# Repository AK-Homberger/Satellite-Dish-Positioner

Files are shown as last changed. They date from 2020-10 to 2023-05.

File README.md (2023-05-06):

# Satellite Dish Positioner

This is an automatical satellite dish positioner with an ESP8266 D1 Mini, a compass and an MPU. It controls the satellite dish direction with a Diseqc rotor (azimut) and a linear actuator (elevation). It uses an gyroscope device for elevation and a compass device for azimut control.

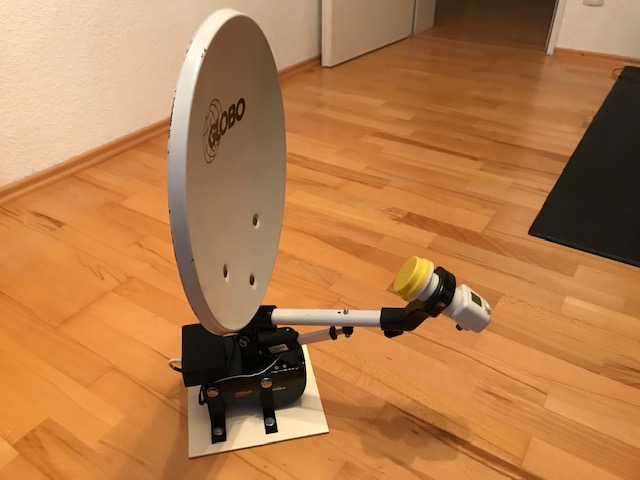
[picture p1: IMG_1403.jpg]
SatPositioner


The purpose of this device is to support me on the boat with the positioning of the satellite dish from the cabin. But it is also usable for campers and mobile homes.

## Hardware
The rotor is a standard Diseqc dish motor for less than 50 Euro. But for this project we use the motor upside down to move the dish in horizontal ballance. We have to remove the cranked dish connection tube from the motor. But keep the bolt and the nut. We need them to connect the upper and lower 3D-printed joint parts. 

The ESP8266 (in D1 Mini) controls the Diseqc motor with 22 kHz tone signals as defined in the [Diseqc specification](https://www.eutelsat.com/files/PDF/DiSEqC-documentation.zip) (see bus_spec.pdf, section 5 and also positioner_appli_notice.pdf). The ESP8266 generates the signal which has to be modulated on the coax signal line of the motor. I found the necessary circuit and signal generator code on GitHub:(https://github.com/acrerd/Arduino-Diseqc-solar-tracker). Many thanks for the helpful support. That saved me a lot of time. For simplification, I only used the right part of the [circuit](https://github.com/AK-Homberger/Satellite-Dish-Positioner/blob/main/diseqc-interface.pdf) starting with the 100 Ohm resistor. The risistor is directly connected to port D5 on the D1 Mini. This is sufficient to generate a signal that the Diseqc motor is recognising.

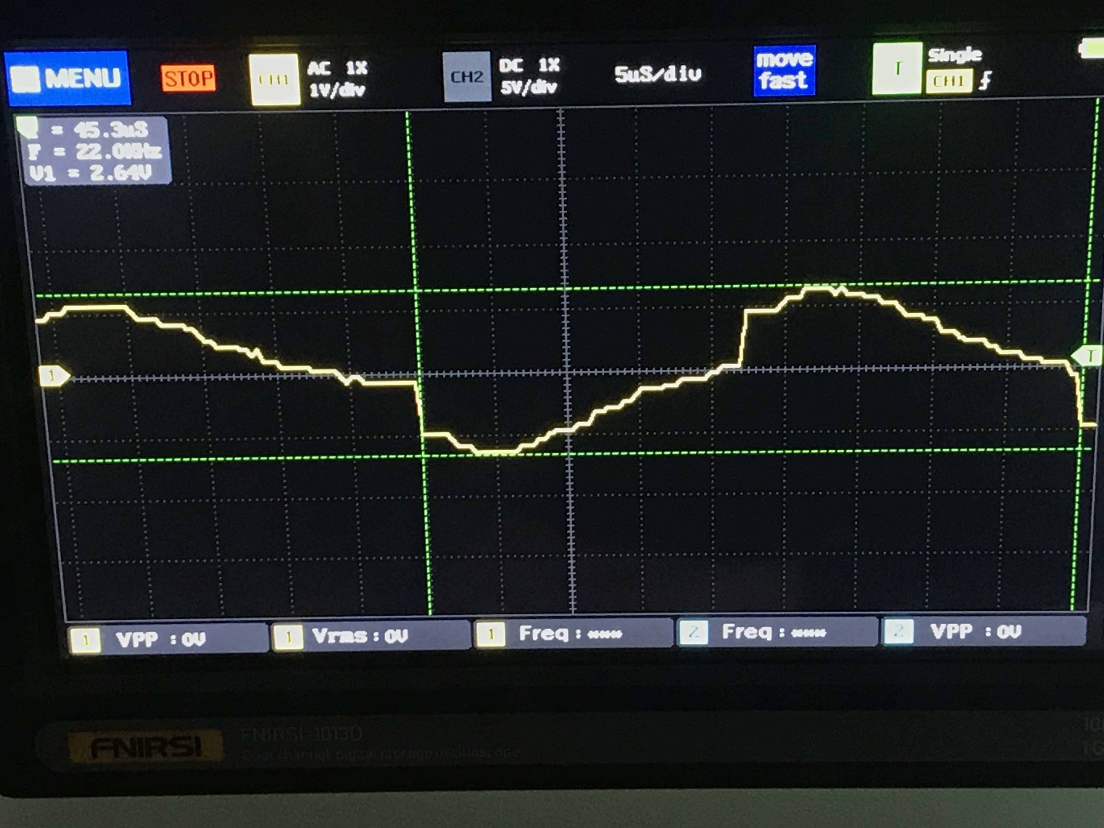
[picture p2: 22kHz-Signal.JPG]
22KhZ-Signal


The delay values in the Arduino code ( functions write0() and write1() ) had to be adjusted for the faster ESP8266. The delay with 21 microseconds works perfectly to generate a 22 kHz signal.

The motor gets the 12 Volt power via the coax connection. Be careful with the coax connector when the device is powerd. A shortcut between core and shield would instantly destroy the inductor coil (it can only handle about 300 mA).

The motor is able to move from -75 to +75 degrees with an accuracy of 1/16 degree. That is more than sufficient for positioning the azimut.
You just have to position the sat finder in a general south facing direction. Thats all.

The elevation is controlled with a standard small linear actuator which is available for less than 30 Euro. I use here an actuator with 50 mm length. But 25 mm should work also.

In addition to the 22 kHz logic, only four other items are required:

- Step-down-converter 12V to 5V: D24V10F5
- Compass: GY-271 from AzDelivery (install [QMC5883LCompass](https://github.com/mprograms/QMC5883LCompass) library in Arduino)
- 6 axis gyroscope: GY-521 from AzDelivery (install [TinyMPU6050](https://github.com/gabriel-milan/TinyMPU6050) library in Arduino):
- Motor driver:  Adafruit DRV8871 DC Motor Driver

**Be careful with the GY-271 from other sources. Some devices are using a HMC5883L compass instead of a QMC5883L. We need the QMC5883L for this project.**

The compass and the gyroscope are connected to the I2C bus of the D1 Mini (using D1=SCL and D2=SDA). The compass is inside the box on the pcb. The gyroscope is connected with a short 4-wire cable and placed on the back of the satellite dish.

The motor driver is using ports D0 and D6. The 22 kHz signal is generated on port D5.

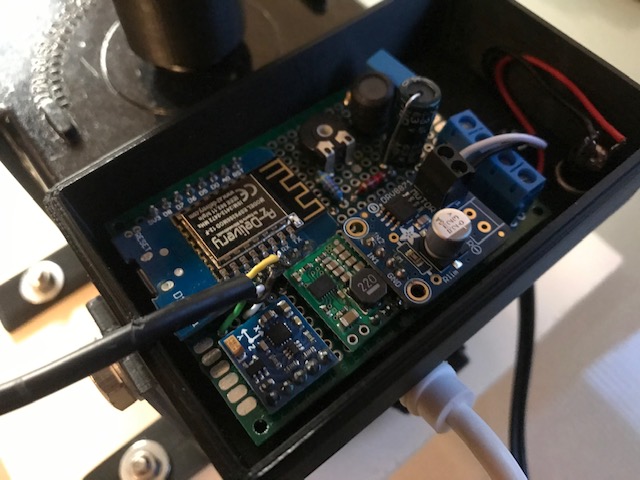
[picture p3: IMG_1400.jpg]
Circuit


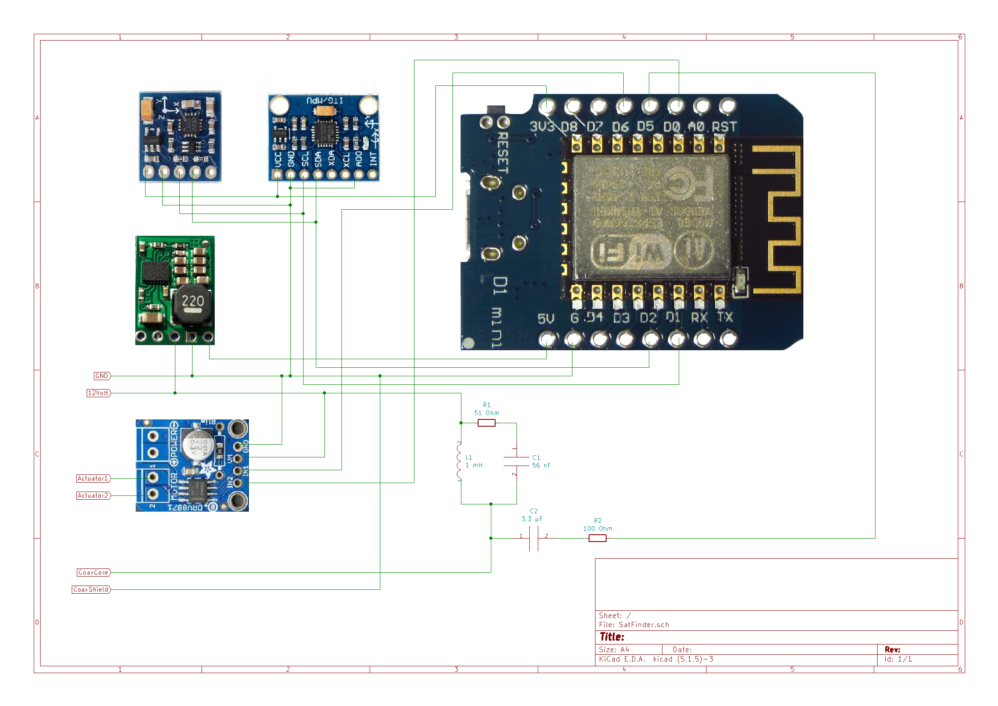
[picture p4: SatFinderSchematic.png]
Schematic


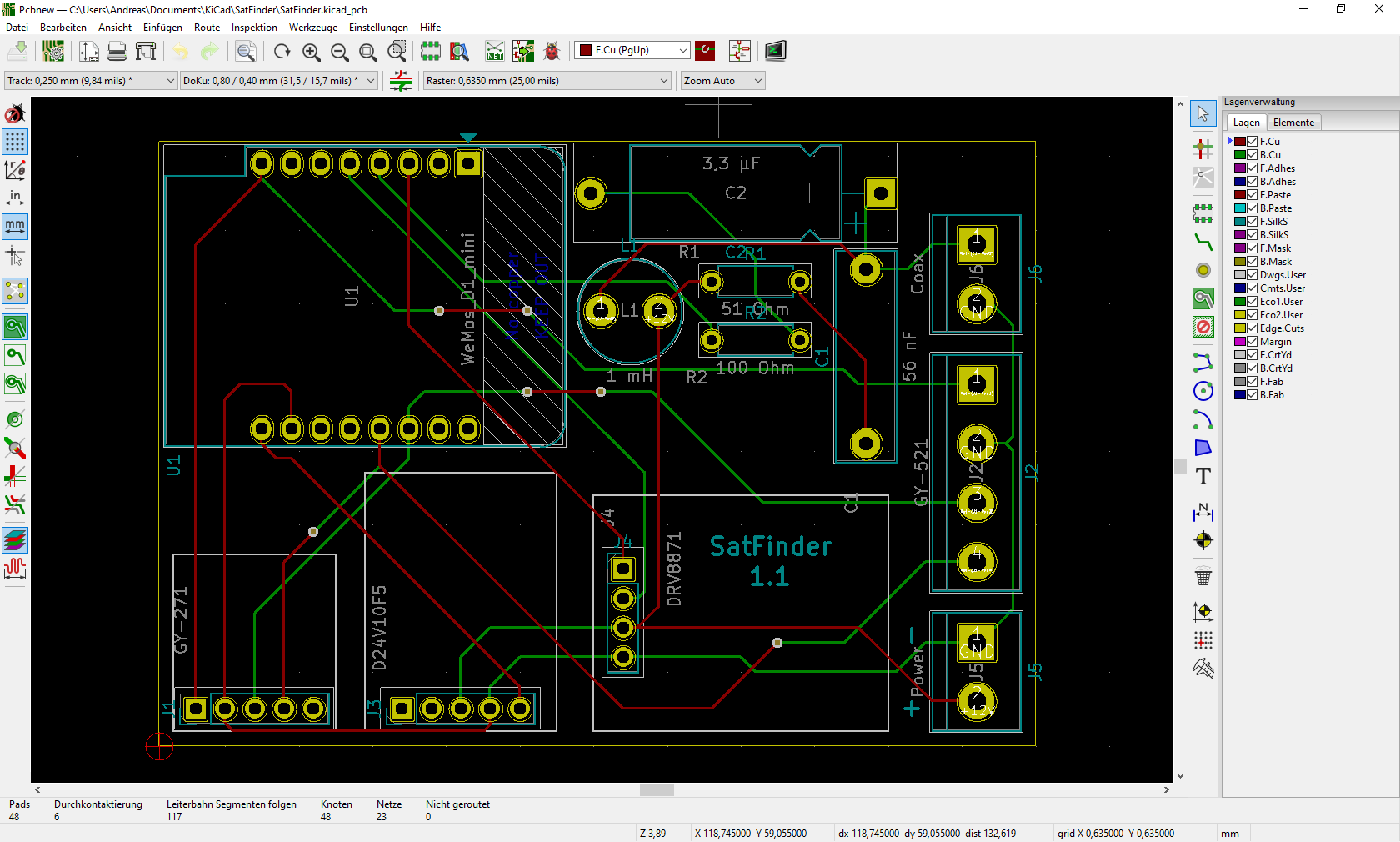
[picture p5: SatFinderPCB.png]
PCB


Schematics and PCB layout is in KiCAD folder.

## Software
The positioner is controlled with a web interface. The ssid and password for WLAN has to be set in the code.

The device is pre-configured for Astra 19.2 and my home location. Please change this for your location and satellite.
You can use one of the free calculators to get the angles for your location and desired setellite (e.g. https://www.satlex.us/en/azel_calc.html). Use "Azimut angle" and "Elevation angle". 

The true north azimut angle needs to be corrected (Az_Offset) to match the magnetic north of the compass (sailors should know how to calculate) and to correct a possible placing error on the pcb. 

The elevation angle must be corrected (El_Offset) with a dish specific value. For my dish this is -18 degrees between dish beam angle and angle of gyroscope mount. The offset has to be calculated only once and defined in the program.

```cpp
//Enter your SSID and PASSWORD
const char* ssid = "ssid";
const char* password = "passwod";

float Astra_Az = 164, Astra_El = 30.19, El_Offset=-18, Az_Offset=-10.0;   // Astra 19.2 position and dish specific offsets
```

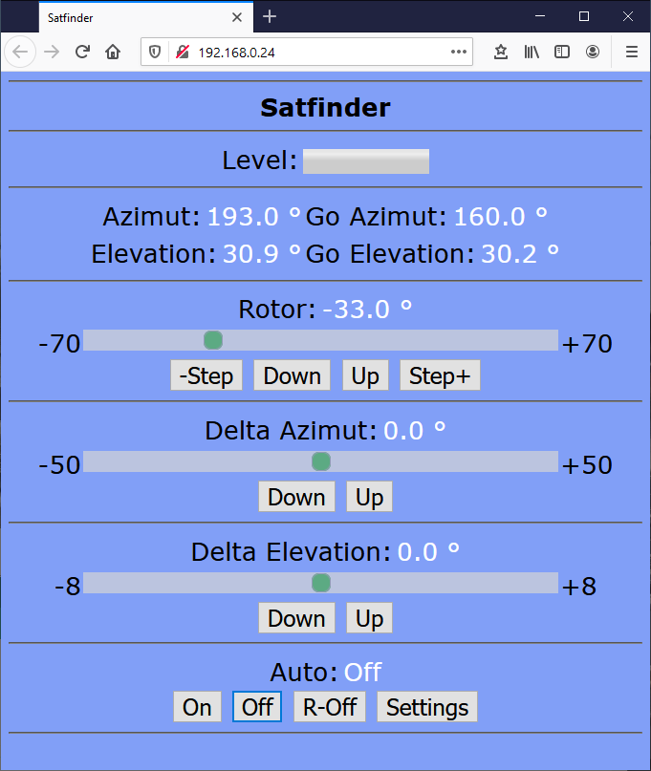
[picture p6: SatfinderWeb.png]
WebInterface


With the web interface you can control the positioner. You can do fine tuning for azimut/elevation and switch automatic control between Off, On and R-Off.

R-Off means automatic control for azimut is switched off. Elevation remains on. This is a kind of "night" mode because the Diseqc motor is a bit noisy when constantly re-positioning. The "-Step/Step+" buttons are changing the rotor for 1/8 degree. Which should be sufficient for the desired purpose. It is possible to change it also to 1/16 degree.

Values for Azimut, Elevation, Offsets and Motor Speed can be changed with a "Settings" web page. Changed values are stored in flash memory (EEPROM) of ESP8266. With "Motor Speed" you can define the speed of the linear actuator. The value should be about 700 and defines the Pulse Width Modulation for the actuator. If the dish begins to "swing" you can adjust the value to avoid this.

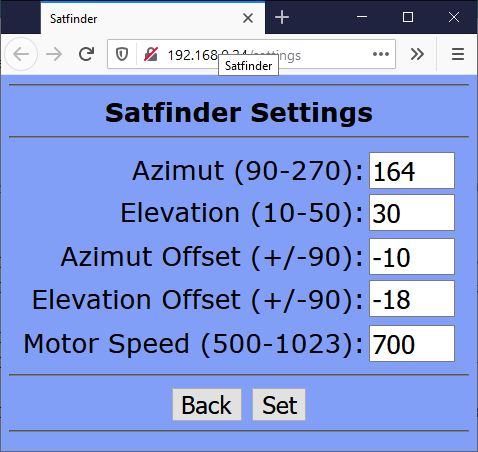
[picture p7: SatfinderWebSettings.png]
Settings
.

To improve the precision of the compass, it is necessary to calibrate the device before using it. To do the calibration, load and run the [calibration sketch](https://github.com/mprograms/QMC5883LCompass/blob/master/examples/calibration/calibration.ino) from the QMC5883L compass library.

During the calibration process the device have to be moved in all possible directions (see library example). It is probably a good idea to do the calibration before placing the pcb on the dish.

The shown six values have to be set in this line:
```
compass.setCalibration(-1598, 1511, -2365, 872, -1417, 1440);   // Do a calibration for the compass and put your values here!!!
```

For the MPU there is also an calibration function available. See library for [details](https://github.com/gabriel-milan/TinyMPU6050/blob/master/examples/ArduinoIDE_Angles_Example/ArduinoIDE_Angles_Example.ino). But due to the fact that the elevation offset has to be set anyway, it is not necessary to do the calibration for the device, to get the individual offsets.

The following line in the code:
```
experimental::ESP8266WiFiGratuitous::stationKeepAliveSetIntervalMs(5000);
```
is part of the internal [ESP8266WiFi](https://github.com/esp8266/Arduino/blob/master/libraries/ESP8266WiFi/src/ESP8266WiFiGratuitous.h) library. It solves a WLAN connection problem for my router by sending ARP packets every 5 seconds to keep the WLAN connection stable.

If you don't need this, simply comment out the line.

## 3D Prints
The connection between the sat dish and the rotor as well as the other parts are designed with OpenSCAD. The files are stored in the SCAD folder.

You can either use the .scad files with OpenSCAD or you can directly print the .stl files stored [here](https://github.com/AK-Homberger/Satellite-Dish-Positioner/tree/main/SCAD/STL).

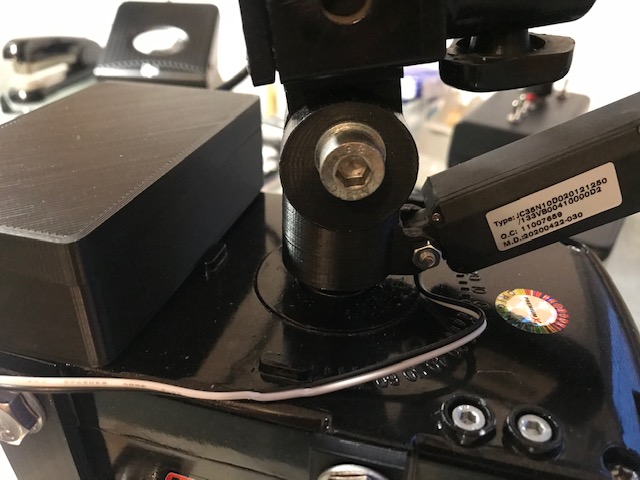
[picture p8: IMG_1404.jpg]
Connection


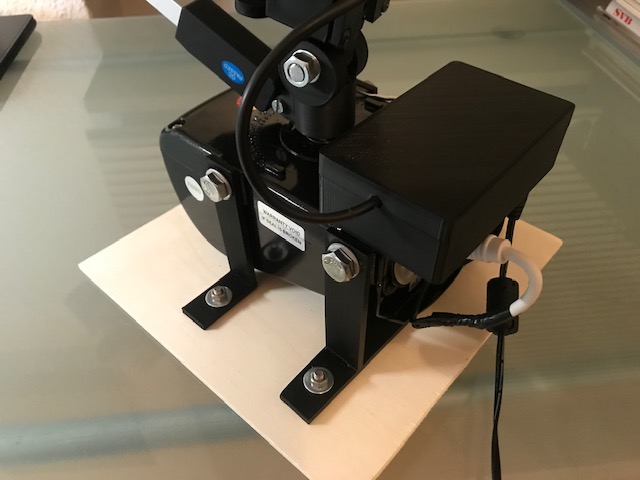
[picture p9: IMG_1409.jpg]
Back


The GY-521 gyroscope is placed on the back of the dish in a hoizonal position. The compass is on the pcb facing to south direction. For other directions do a correction in the code with "#define Az_PCB_Correction 90". I had to add 90 degrees to get south direction, 180°.

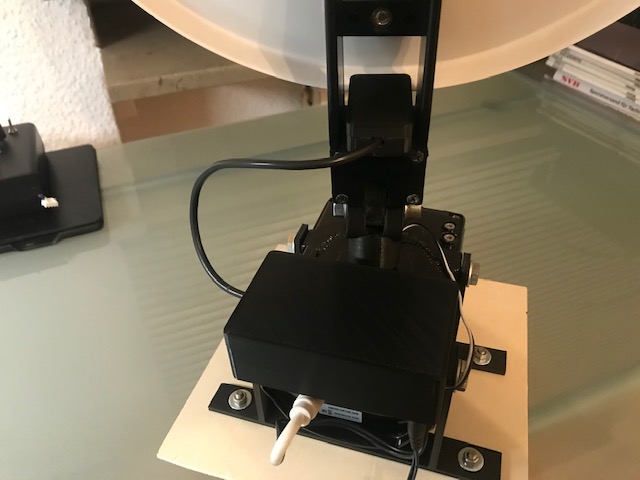
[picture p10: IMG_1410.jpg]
Gyroscope


The connection between the dish and the Diseqc motor has to be very stable. I used 0.2 mm accuracy and 70% fillrate for PLA. Use of ABS is also an option.

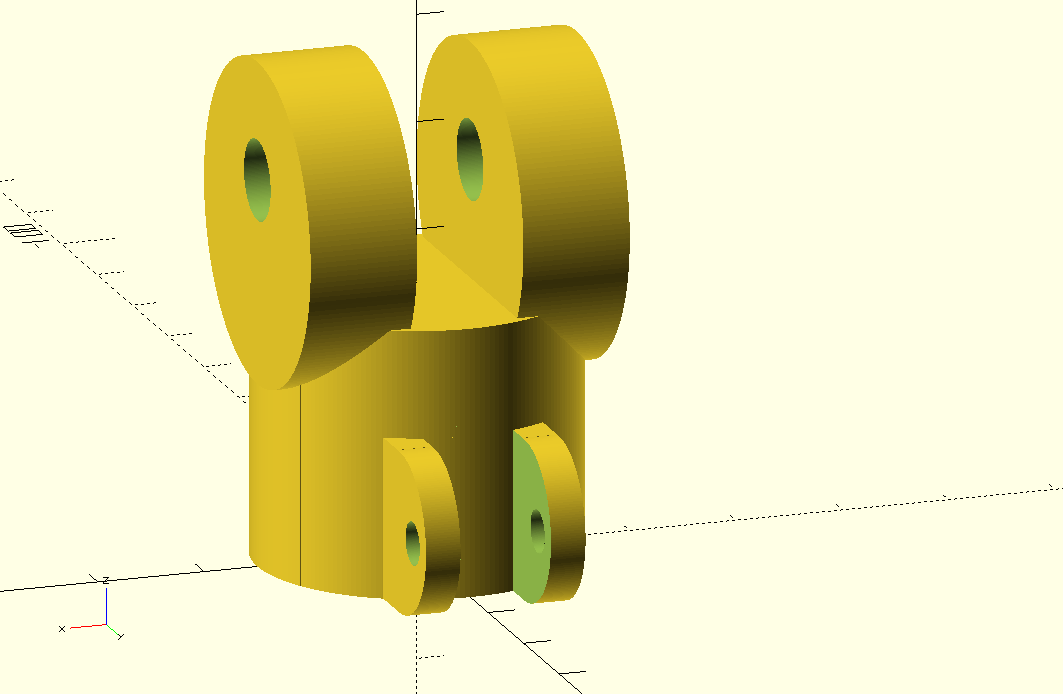
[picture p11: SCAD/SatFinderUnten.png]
Bottom


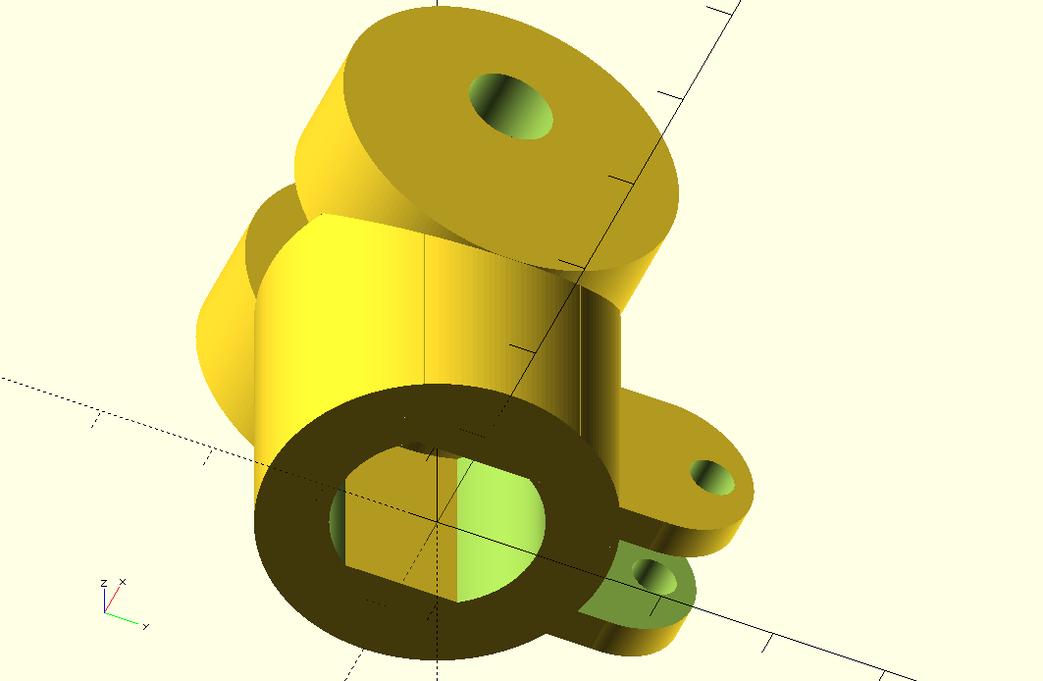
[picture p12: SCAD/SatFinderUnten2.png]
Bottom2


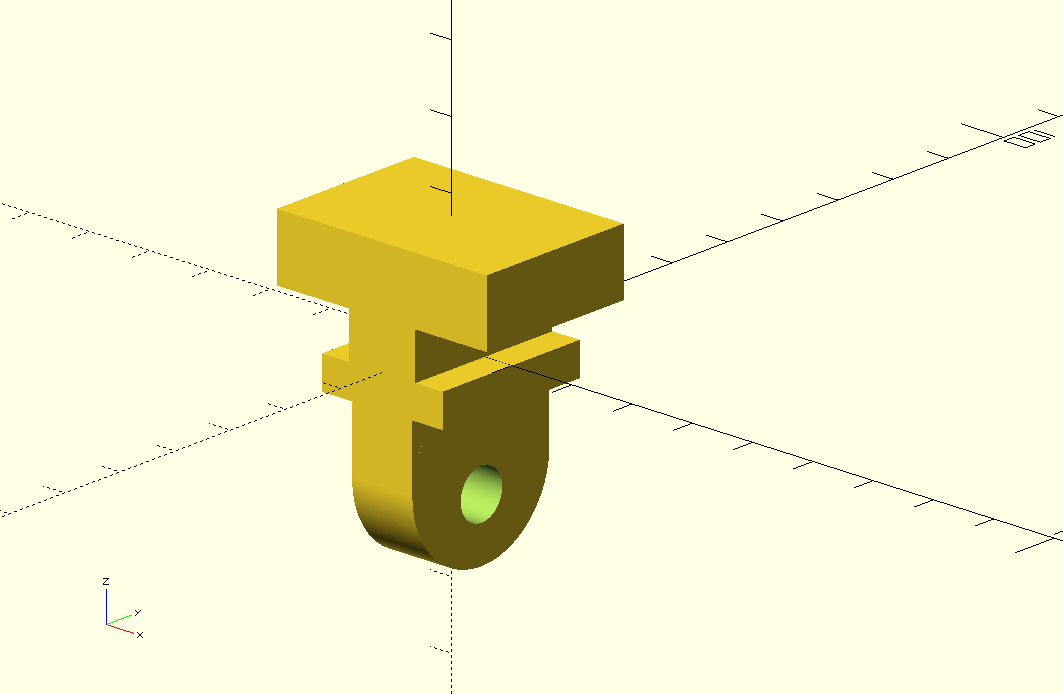
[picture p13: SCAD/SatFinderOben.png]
Top


## Parts
- Sat dish: [Link](https://www.voelkner.de/products/21807/Telestar-5103309-Camping-SAT-Anlage-ohne-Receiver-Teilnehmer-Anzahl-1.html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)
- Diseqc motor: [Link](https://www.ebay.de/itm/332284938131?itemid=332284938131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) or [Link](https://www.wiltanet.de/sat-empfang/diseqc-schalter-motor/diseqc-motor/diseqc-motor/a-120017)
- Linear Actuator (25 or 50 mm): [Link](https://www.ebay.de/itm/750N-25-150-mm-Linear-Actuator-elektrische-Mikro-Linearantrieb-12V-Kraft-IP65/402438285052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)
- D1 Mini: AzDelivery (e.g. on Amazon) [Link](https://www.amazon.de/stores/AZDelivery/AZDelivery/page/2DB821D9-4A4B-4FD2-A50B-AE111B57FC93)
- GY-271 compass: AzDelivery (e.g. on Amazon) [Link](https://www.amazon.de/stores/AZDelivery/AZDelivery/page/2DB821D9-4A4B-4FD2-A50B-AE111B57FC93) or [Link](https://www.makershop.de/sensoren/gy-271-hmc5883l/)
- GY-521 gyroscope: AzDelivery (e.g. on Amazon) [Link](https://www.amazon.de/stores/AZDelivery/AZDelivery/page/2DB821D9-4A4B-4FD2-A50B-AE111B57FC93)
- D24V10F5 [Link](https://eckstein-shop.de/Pololu-5V-1A-Step-Down-Spannungsregler-D24V10F5)
- Adafruit DRV8871: [Link](https://eckstein-shop.de/Adafruit-DRV8871-DC-Motor-Driver-Breakout-Board-36A-Max)
- Resistor 51 Ohm [Link](https://www.reichelt.de/de/en/carbon-film-resistor-1-4-w-5-51-ohm-1-4w-51-p1441.html?&nbc=1)
- Resistor 100 Ohm [Link](https://www.reichelt.de/de/en/carbon-film-resistor-1-4-w-5-100-ohms-1-4w-100-p1336.html?&nbc=1)
- Inductor 1 mH - BOU RLB0914-102K [Link](https://www.reichelt.de/index.html?ACTION=446&LA=0&nbc=1&q=bou%20rlb0914-102k)
- Capacitor 56 nF - RND 150MKT563K2E [Link](https://www.reichelt.de/index.html?ACTION=446&LA=0&nbc=1&q=150mkt563k2e%20) or alternative MKP-X2 56N2 [Link](https://www.reichelt.de/de/en/radio-interference-suppression-capacitors-56nf-305v-rm15-mkp-x2-56n2-p173414.html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)
- Capacitor 3,3 µF - TON 3,3/63 [Link](https://www.reichelt.de/index.html?ACTION=446&LA=446&nbc=1&q=ton%203%2C3%2F63)
- Connector 2-pin (*2) [Link](https://www.reichelt.de/de/en/2-pin-terminal-strip-spacing-5-08-akl-101-02-p36605.html?&nbc=1)
- Connector 4-pin [Link](https://www.reichelt.de/de/en/4-pin-terminal-strip-spacing-5-08-akl-101-04-p36607.html?&nbc=1)
- DC Jack [Link](https://www.reichelt.de/de/en/connector-dc-female-bulkhead-delock-89911-p259483.html?&nbc=1)

## Updates
- Version 1.1 - 19.05.2021: Improved 22 kHz signal generation (Issue #5).
- Version 1.0 - 09.02.2021: Added pcb mount correction value. Release version 1.0
- Version 0.6 - 05.02.2021: Added settings page and storage of settings in flash memory.
- Version 0.5 - 07.11.2020: Corrected error in azimut calculation (boundary check 0-360).
- Version 0.4 - 06.11.2020: Changed PCB layout to version 1.1. Larger terminal strips (5.08 mm).
- Version 0.4 - 28.10.2020: Added permanent azimut offset.
- Version 0.3 - 26.10.2020: Separated elevation and elevation offset to work with true elevation angles from calculators. 
- Version 0.2 - 26.10.2020: Initial version.

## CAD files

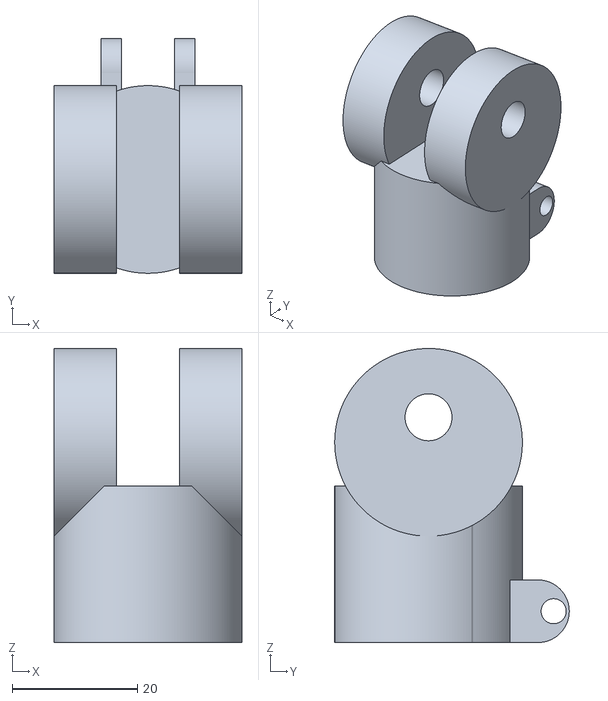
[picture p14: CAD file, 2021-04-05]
SCAD/STL/SatFinderUnten.stl
30.0 x 37.5 x 47.0

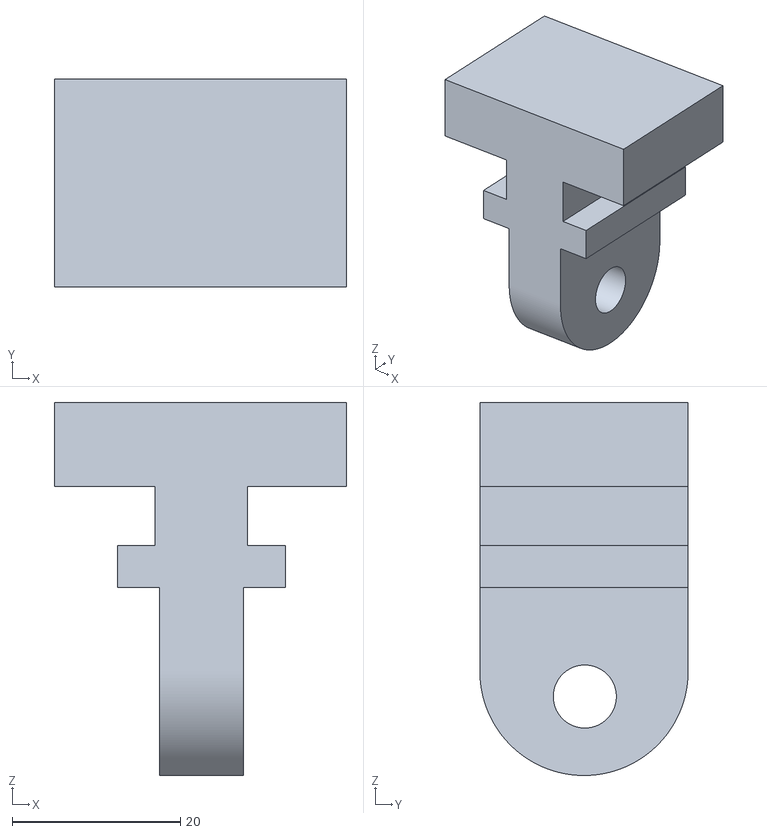
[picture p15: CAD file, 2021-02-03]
SCAD/STL/SatFinderOben.stl
34.8 x 24.8 x 44.4

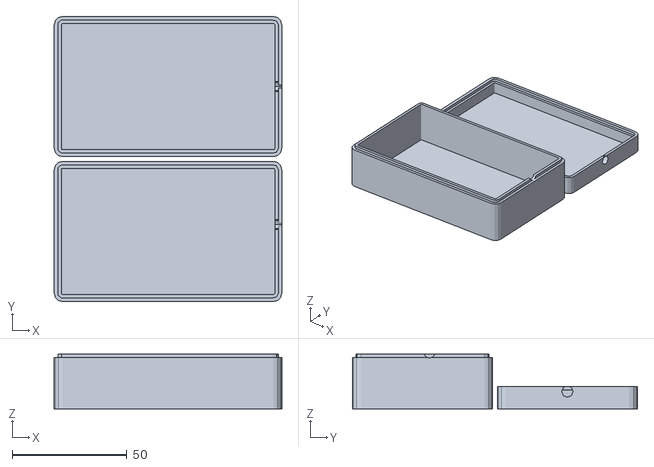
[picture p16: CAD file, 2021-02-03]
SCAD/STL/Case1.stl
99.0 x 124.0 x 23.8

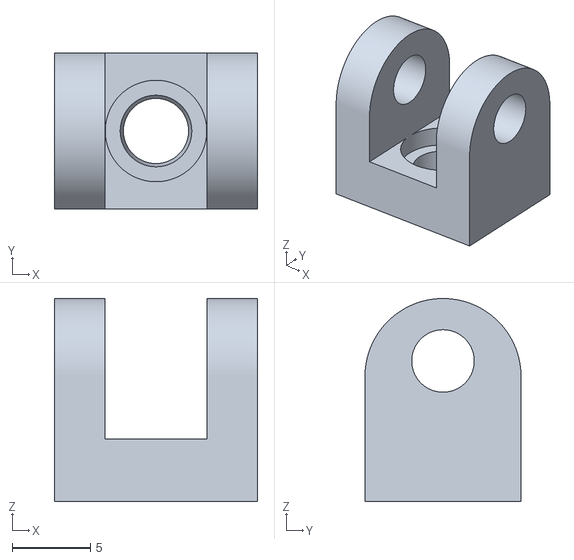
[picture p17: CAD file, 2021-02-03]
SCAD/STL/Halter3.stl
13.0 x 10.0 x 13.0

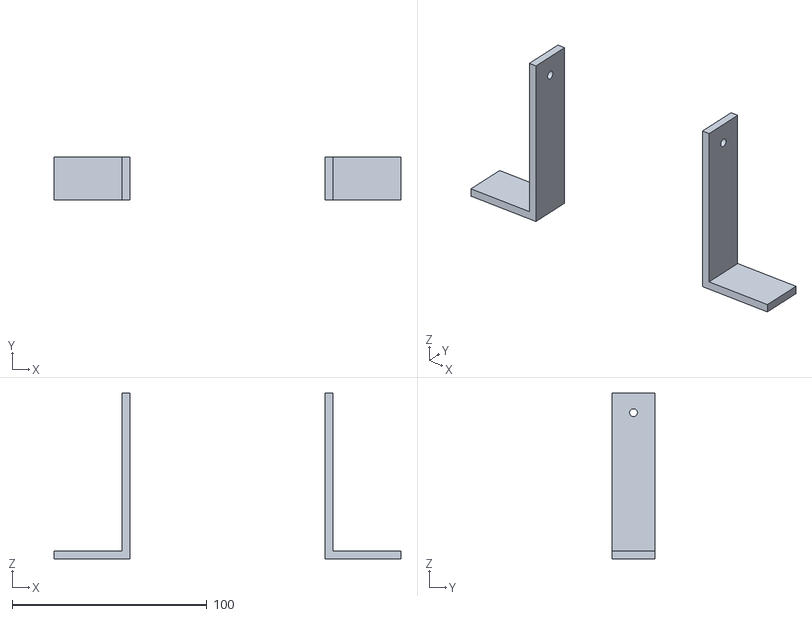
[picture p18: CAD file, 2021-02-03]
SCAD/STL/Stand2.stl
178.0 x 22.0 x 85.0

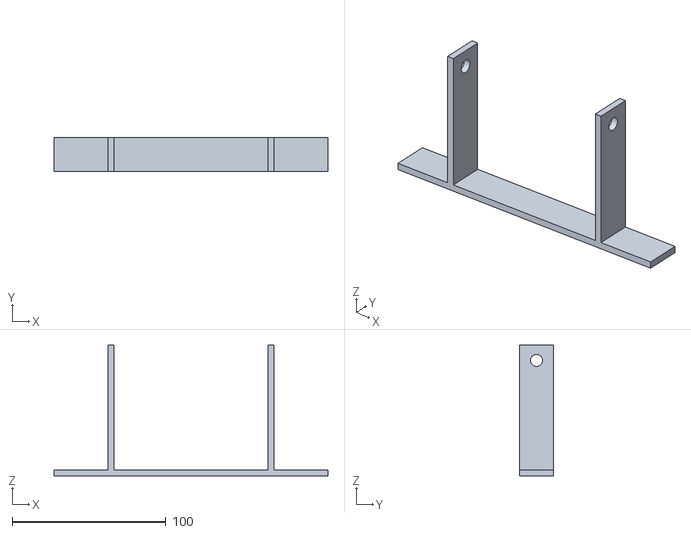
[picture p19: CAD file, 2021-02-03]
SCAD/STL/Stand.stl
178.0 x 22.0 x 85.0

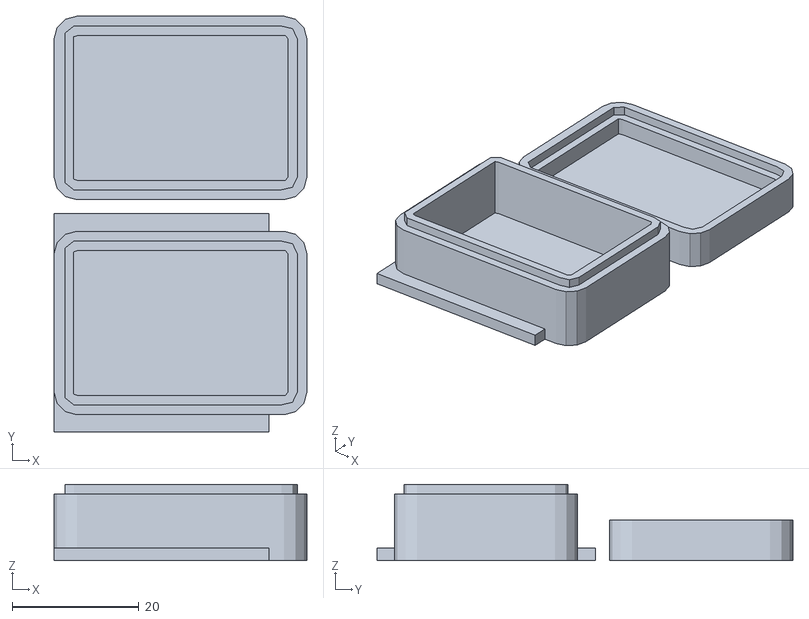
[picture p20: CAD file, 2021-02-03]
SCAD/STL/Case-LageS.stl
40.0 x 65.7 x 12.1

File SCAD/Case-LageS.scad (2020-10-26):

/*!
@brief Generic Electronic Device packaging for Tyndall
@details This OpenSCAD script will generate a 2 part fit together packaging.
This starts by making a pair of hollow rounded cuboids by differencing a slightly smaller one from a slightly larger one
then it will also remove another small amount of material to make a lip
one of the objects will have an internal lip the other one will have an external lip
you will be able to specify fit type
It can also create simple square or cylindrical cutouts on any face of the top or bottom half
4 cylindrical support posts can also be added on the bottom or top half to help position a PCB or similar device
all these features can be controlled from the variables section

@author Mark Gaffney
@version 1.6
@date 2012-05-29

@todo
enable for measurements from corners or centres of faces etc
add "fit factor" for cutouts
add option for connecting struts between top and bottom in side by side mode
re-incorporate some advanced features from v1.5

@warning
@note
Changes from previous versions:

v1.6
 - 	Incorporates improvements from brians physiological health board case v2.6
 - - 	better support for adding parts, changing features and changing layout using control variables
 - - 	Can select how tall the 2 halves are relative to each other
 - - 	Added method to choose whether to have fully cut or covered cutouts
 - -	Added optional mouse-ears
 - 	more logical method for creating circular and square cutouts in preparation for array based system
 - 	simplified method for controlling lip tolerance
 - 	abandoned some features from v1.5 such as profiled lips in quest for simplicity
 - 	method optionally adding posts to top and bottom
 - 	variables for controlling support posts on top and bottom separately
 - 	pasted contents of mouse ears and rounded cuboid as modules rather than accessing them as external files

v1.5
	adjusted a few values after receiving SLA proto-types
	increased height of posts
	added support structures on top side
	decrease diameter of support structures on top side slightly to allow for brackets at end of 40 way
	decreased z clearance
	removed includes/uses needed for WIMU packaging
	
v1.4
	added angled lip (Cube_cone_cylinder_minkowski sum) for better mating of top and bottom parts when made via SLA/SLS etc
	new more simplistic rounded cuboid module
	moved around the cutout for the uUSB so that there wasn't such a thin peice of plastic above it
changed post type to nub as SLA should be able to handle the resolution
	added easier control of orientation of parts relative to each other using single variable side_by_side
	added axis labels to most faces and tyndall logo to bottom
	added new fit type for super accurate manufacturing techniques such as SLA
v1.3
	Fix cutout positions for TOP SQUARE East and BOTTOM SQUARE West side
	Fix position of base of support posts on bottom half
v1.2
	Fixed Inner and Outer Lip Clearance implementation
	Added ability to generate support posts on bottom half of either nub or screw hole type
v1.1
	???This version was lost in a computer crash. GRRRR!
	???It implemented the ability to choose the reference point for measurements for each side
	???Let this be a lesson!
	???Back your stuff up regularly and on separate devices!
v 1.0
	Ensure pcb_clearance and fit clearance is taken into account
	fit type values changed
		force_fit from 0.4 to 0.2
		hold_fit from 0.6 to 0.3
		slide_fit from 0.8 to 0.4
		free_fit from 1to 0.5
	add cylinder & square holes to all faces
	allowed to stack or see side by side
	replace 0.1s with a_bit
	check holes on top & bottom sides meet properly
*/

//*********includes********

//use <mouse_ears_test.scad>;//mouse_ears (total_x, total_y, 2*z_resolution, mouse_ear_diameter);
//use <rounded_cuboid_v2.5.scad>;//rounded_cuboid_2_5(tot_l, tot_b, tot_h, tot_r, tot_s,center=true/false,use_sphere,top_n_bottom); hollow_rounded_cuboid_2_5(tot_l, tot_b, tot_h, tot_r, tot_s, wall_t,center=true/false,use_sphere,top_n_bottom);

//*************Control*Variables****************

has_mouse_ears=0;
has_bottom=1;
has_top=1;
has_posts=0;
posts_on_top=1;
posts_on_bottom=1;
is_side_by_side=1;
has_device=0;// for optionally showing an imported model of the internal device, not used here
device_on_top=0;
//has_switch=0; //for optionally showing an imported part, not used here
//simple_lip=0;//for choosing if a simple (1) or locking type lip (0) is used between the 2 halves, not used yet

//***********Pre*Defined*Variables**************

z_resolution=0.32;//this is how thick your printed layers are
xy_resolution=0.5;//how thick is an extruder filament in XY plane

//clearances for the interlocking lips on 3d printed parts, these values will depend on the printer it is made on. Users should NOT change these
super_fit=0.0;//
force_fit=0.2; //!@param force_fit, this is the separation between surfaces that will give a tight fit
hold_fit=0.3; //this is the separation between surfaces that will give a fit that will hold itself together but be easy to remove
slide_fit=0.4; //this is the separation between surfaces that will give a free moving fit without much wobble
free_fit=0.5; //this is the separation between surfaces that will give a free moving & loose but easy to assemble fit

//fudge
a_bit=0.1; //This is used to move items, oversize or undersize them by small amount to maintain manifoldness of the generated 3d shape, this should be on the order of 10% of the smallest dimension you will plan to use 

//**************User*Variables*****************

//internal dimensions
int_l_holder=31;//max length of the item to be held internally
int_b_holder=20;//max breadth of the item to be held internally
int_h_holder=10;//max height of the item to be held internally
int_r_holder=0.5;//radius of the corners of the device to be held internally
int_tol_holder=1.5;//distance between internal walls and edges of the item to be held internally, this allows for devices that may not be accurately measured or made and should generally be >0.5mm
int_r_tol_holder=0.1;//tolerance for the internal corners
curve_f_holder=3;//how many facets do the curved corners have?
wall_t_holder=3;//how thick are the vertical walls?
base_t_holder=2;//how thick is the base?

//lip dimensions
lip_h=1.5;//how tall are the interlocking lips?
lip_fit=super_fit;//what is the tolerance for the fit between the two sets of interlocking lips?
lip_t= wall_t_holder/2-lip_fit;//automatically calculated lip thickness (width)

//external dimensions
ext_l_holder=int_l_holder+2*(int_tol_holder+wall_t_holder);
ext_b_holder=int_b_holder+2*(int_tol_holder+wall_t_holder);
ext_h_holder=int_h_holder+2*int_tol_holder+2*base_t_holder;
ext_r_holder=int_r_holder+int_r_tol_holder+wall_t_holder;
bottom_top_int_h_ratio=0.22;//how tall is the internal void of the bottom section relative to the top section (0.5 would give 2 halves of equal height)
bottom_h=(int_h_holder*bottom_top_int_h_ratio)+int_tol_holder+base_t_holder+lip_h/2;//how tall is the bottom half
top_h=ext_h_holder-bottom_h+lip_h;//how tall is the top half

//features
mouse_ear_diameter=12;
mouse_ear_thickness=2*z_resolution;
side_side_separation=5;//how far apart the two halves are if generated together


//cutout variables
cutout_wall_thickness=1*xy_resolution; //how thick is the plastic left in the cutouts on the sides? set to 0 if you do not want any plastic left in these cutouts
cutout_base_thickness=2*z_resolution;//how thick is the plastic left in the cutouts on the bottom or top? set to 0 if you do not want any plastic left in these cutouts

north_cutout=0;//if 1 cutout on this side else none
n_cutout_c=1;//if 1 gives circle just using the _r value and ignoring the others, else gives rounded square
n_cutout_l=10;//length/tallness of the cutout
n_cutout_b=22;//breadth of the cutout
n_cutout_h=wall_t_holder+2*a_bit;//basically wall thickness plus a bit
n_cutout_r=2;//radius of the corners of the cutout
n_cutout_e=4;//height of the bottom of the cutout above the bottom of the holder 
n_cutout_t=20;//translation along the face -left +right as you look at the face from outside

south_cutout=0;//if 1 cutout on this side else none
s_cutout_c=1;//if 1 gives circle just using the _r value and ignoring the others, else gives rounded square
s_cutout_l=8;//length/tallness of the cutout
s_cutout_b=11;//breadth of the cutout
s_cutout_h=wall_t_holder+2*a_bit;//basically wall thickness plus a bit
s_cutout_r=2;//radius of the corners of the cutout
s_cutout_e=s_cutout_l+(-int_h_holder -lip_h)/2-int_tol_holder -1;//height of the bottom of the cutout above the bottom of the holder 
s_cutout_t=-1;//translation along the face -left +right
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

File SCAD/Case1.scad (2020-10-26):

/*!
@brief Generic Electronic Device packaging for Tyndall
@details This OpenSCAD script will generate a 2 part fit together packaging.
This starts by making a pair of hollow rounded cuboids by differencing a slightly smaller one from a slightly larger one
then it will also remove another small amount of material to make a lip
one of the objects will have an internal lip the other one will have an external lip
you will be able to specify fit type
It can also create simple square or cylindrical cutouts on any face of the top or bottom half
4 cylindrical support posts can also be added on the bottom or top half to help position a PCB or similar device
all these features can be controlled from the variables section

@author Mark Gaffney
@version 1.6
@date 2012-05-29

@todo
enable for measurements from corners or centres of faces etc
add "fit factor" for cutouts
add option for connecting struts between top and bottom in side by side mode
re-incorporate some advanced features from v1.5

@warning
@note
Changes from previous versions:

v1.6
 - 	Incorporates improvements from brians physiological health board case v2.6
 - - 	better support for adding parts, changing features and changing layout using control variables
 - - 	Can select how tall the 2 halves are relative to each other
 - - 	Added method to choose whether to have fully cut or covered cutouts
 - -	Added optional mouse-ears
 - 	more logical method for creating circular and square cutouts in preparation for array based system
 - 	simplified method for controlling lip tolerance
 - 	abandoned some features from v1.5 such as profiled lips in quest for simplicity
 - 	method optionally adding posts to top and bottom
 - 	variables for controlling support posts on top and bottom separately
 - 	pasted contents of mouse ears and rounded cuboid as modules rather than accessing them as external files

v1.5
	adjusted a few values after receiving SLA proto-types
	increased height of posts
	added support structures on top side
	decrease diameter of support structures on top side slightly to allow for brackets at end of 40 way
	decreased z clearance
	removed includes/uses needed for WIMU packaging
	
v1.4
	added angled lip (Cube_cone_cylinder_minkowski sum) for better mating of top and bottom parts when made via SLA/SLS etc
	new more simplistic rounded cuboid module
	moved around the cutout for the uUSB so that there wasn't such a thin peice of plastic above it
changed post type to nub as SLA should be able to handle the resolution
	added easier control of orientation of parts relative to each other using single variable side_by_side
	added axis labels to most faces and tyndall logo to bottom
	added new fit type for super accurate manufacturing techniques such as SLA
v1.3
	Fix cutout positions for TOP SQUARE East and BOTTOM SQUARE West side
	Fix position of base of support posts on bottom half
v1.2
	Fixed Inner and Outer Lip Clearance implementation
	Added ability to generate support posts on bottom half of either nub or screw hole type
v1.1
	???This version was lost in a computer crash. GRRRR!
	???It implemented the ability to choose the reference point for measurements for each side
	???Let this be a lesson!
	???Back your stuff up regularly and on separate devices!
v 1.0
	Ensure pcb_clearance and fit clearance is taken into account
	fit type values changed
		force_fit from 0.4 to 0.2
		hold_fit from 0.6 to 0.3
		slide_fit from 0.8 to 0.4
		free_fit from 1to 0.5
	add cylinder & square holes to all faces
	allowed to stack or see side by side
	replace 0.1s with a_bit
	check holes on top & bottom sides meet properly
*/

//*********includes********

//use <mouse_ears_test.scad>;//mouse_ears (total_x, total_y, 2*z_resolution, mouse_ear_diameter);
//use <rounded_cuboid_v2.5.scad>;//rounded_cuboid_2_5(tot_l, tot_b, tot_h, tot_r, tot_s,center=true/false,use_sphere,top_n_bottom); hollow_rounded_cuboid_2_5(tot_l, tot_b, tot_h, tot_r, tot_s, wall_t,center=true/false,use_sphere,top_n_bottom);

//*************Control*Variables****************

has_mouse_ears=0;
has_bottom=1;
has_top=1;
has_posts=0;
posts_on_top=1;
posts_on_bottom=0;
is_side_by_side=1;
has_device=0;// for optionally showing an imported model of the internal device, not used here
device_on_top=0;
//has_switch=0; //for optionally showing an imported part, not used here
//simple_lip=0;//for choosing if a simple (1) or locking type lip (0) is used between the 2 halves, not used yet

//***********Pre*Defined*Variables**************

z_resolution=0.32;//this is how thick your printed layers are
xy_resolution=0.5;//how thick is an extruder filament in XY plane

//clearances for the interlocking lips on 3d printed parts, these values will depend on the printer it is made on. Users should NOT change these
super_fit=0.0;//
force_fit=0.2; //!@param force_fit, this is the separation between surfaces that will give a tight fit
hold_fit=0.3; //this is the separation between surfaces that will give a fit that will hold itself together but be easy to remove
slide_fit=0.4; //this is the separation between surfaces that will give a free moving fit without much wobble
free_fit=0.5; //this is the separation between surfaces that will give a free moving & loose but easy to assemble fit

//fudge
a_bit=0.1; //This is used to move items, oversize or undersize them by small amount to maintain manifoldness of the generated 3d shape, this should be on the order of 10% of the smallest dimension you will plan to use 

//**************User*Variables*****************

//internal dimensions
int_l_holder=90;//max length of the item to be held internally
int_b_holder=52;//max breadth of the item to be held internally
int_h_holder=25;//max height of the item to be held internally
int_r_holder=0.5;//radius of the corners of the device to be held internally
int_tol_holder=1.5;//distance between internal walls and edges of the item to be held internally, this allows for devices that may not be accurately measured or made and should generally be >0.5mm
int_r_tol_holder=0.1;//tolerance for the internal corners
curve_f_holder=3;//how many facets do the curved corners have?
wall_t_holder=3;//how thick are the vertical walls?
base_t_holder=2;//how thick is the base?

//lip dimensions
lip_h=1.5;//how tall are the interlocking lips?
lip_fit=super_fit;//what is the tolerance for the fit between the two sets of interlocking lips?
lip_t= wall_t_holder/2-lip_fit;//automatically calculated lip thickness (width)

//external dimensions
ext_l_holder=int_l_holder+2*(int_tol_holder+wall_t_holder);
ext_b_holder=int_b_holder+2*(int_tol_holder+wall_t_holder);
ext_h_holder=int_h_holder+2*int_tol_holder+2*base_t_holder;
ext_r_holder=int_r_holder+int_r_tol_holder+wall_t_holder;
bottom_top_int_h_ratio=0.22;//how tall is the internal void of the bottom section relative to the top section (0.5 would give 2 halves of equal height)
bottom_h=(int_h_holder*bottom_top_int_h_ratio)+int_tol_holder+base_t_holder+lip_h/2;//how tall is the bottom half
top_h=ext_h_holder-bottom_h+lip_h;//how tall is the top half

//features
mouse_ear_diameter=12;
mouse_ear_thickness=2*z_resolution;
side_side_separation=2;//how far apart the two halves are if generated together


//cutout variables
cutout_wall_thickness=0*xy_resolution; //how thick is the plastic left in the cutouts on the sides? set to 0 if you do not want any plastic left in these cutouts
cutout_base_thickness=2*z_resolution;//how thick is the plastic left in the cutouts on the bottom or top? set to 0 if you do not want any plastic left in these cutouts

north_cutout=1;//if 1 cutout on this side else none
n_cutout_c=1;//if 1 gives circle just using the _r value and ignoring the others, else gives rounded square
n_cutout_l=10;//length/tallness of the cutout
n_cutout_b=22;//breadth of the cutout
n_cutout_h=wall_t_holder+2*a_bit;//basically wall thickness plus a bit
n_cutout_r=2.5;//radius of the corners of the cutout
n_cutout_e=4;//height of the bottom of the cutout above the bottom of the holder 
n_cutout_t=0;//translation along the face -left +right as you look at the face from outside

south_cutout=0;//if 1 cutout on this side else none
s_cutout_c=0;//if 1 gives circle just using the _r value and ignoring the others, else gives rounded square
s_cutout_l=8;//length/tallness of the cutout
s_cutout_b=11;//breadth of the cutout
s_cutout_h=wall_t_holder+2*a_bit;//basically wall thickness plus a bit
s_cutout_r=2;//radius of the corners of the cutout
s_cutout_e=s_cutout_l+(-int_h_holder -lip_h)/2-int_tol_holder -1;//height of the bottom of the cutout above the bottom of the holder 
s_cutout_t=-1;//translation along the face -left +right
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

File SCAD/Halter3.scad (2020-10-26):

difference(){
    difference(){
    difference(){
         union(){
            cube([13, 10, 8]);
            translate([0, 10/2, 8]){
                rotate([0, 90, 0]){
                cylinder(h = 13, r1=10/2, r2 =10/2, $fn=200);     
                }
            }    
        }
            
        translate([3.25, -1, 4]){
            cube([6.5, 17, 15]);
            }    
        }
        translate([-1, 10/2, (13+5)/2]){
            rotate([0, 90, 0]){
                cylinder(h = 17, r1=4/2, r2 =4/2, $fn=200); 
            }
        }
    }
    translate([13/2, 10/2 , -1]){
        cylinder(h = 6, r1=4/2, r2 =5/2, $fn=200);
        
    }  
    translate([13/2, 10/2 , 2.5]){
        cylinder(h = 2, r1=6.5/2, r2 =6.5/2, $fn=200);
    }
}

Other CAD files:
SCAD/SatFinderOben.scad
SCAD/SatFinderUnten.scad
SCAD/Stand.scad
SCAD/Stand2.scad

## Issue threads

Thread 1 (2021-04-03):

56nF capacitor no longer available

luftpumpe83, 2021-04-03:
The capacitor C1 (56nF) is no longer available at Reichelt. It's also hard to get anywhere else.
Is it possible to use this one instead: https://www.reichelt.de/funkentstoerkondensator-x2-56-nf-305-v-rm-10-0-105-c-10--mkp-x2-56n-p173413.html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
Thank you!

AK-Homberger, 2021-04-04:
Hi,
thanks for reporting the availability issue for the capacitor. Electrically your alternative would work. But it has a shorter distance between the pins (10 mm instead of 15 mm). I will try to find a a fitting alternative or I will update the PCB for your alternative capacitor with 10 mm distance.
Regards,
Andreas

AK-Homberger, 2021-04-04:
This alternative will work with the current PCB layout: https://www.reichelt.de/de/en/radio-interference-suppression-capacitors-56nf-305v-rm15-mkp-x2-56n2-p173414.html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

Closed 2021-04-04.

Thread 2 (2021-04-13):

code for access point

luftpumpe83, 2021-04-13:
Hi,
could you please also upload a changed version of your sketch to work as an access point?
I've tried on my own with code samples I've found on several websites but can't get it working. I'm no programmer ;)
This would be very nice of you.
Thanks in advance!

AK-Homberger, 2021-04-14:
Hi,

PLease have a look to the Anchor Chain Remote Code: https://github.com/AK-Homberger/ESP8266_AnchorChainControl_WLAN

You can use the same WiFi Code to implement the AP function for the Satellite Sketch.

Regards,
Andreas

luftpumpe83, 2021-04-14:
Hi,
thank you so much. It's working!
Regards,
Olli

Closed 2021-04-14.

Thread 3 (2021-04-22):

Use stepper motors instead of Diseqc motors

WK-Eider, 2021-04-22:
I have a fully automatic satellite dish, unfortunately with water damage and the electronics are defective.
Now I want to use your solution. Unfortunately I have a stepper motor for each level.
For the elevation I will be able to convert the sketch for a stepper motor. But with the azimuth drive, a lot is done in the Diseqc motor module. I'm not quite sure about that yet.
Is there any further information?
Or do you have any tips for me?
Thanks !!

AK-Homberger, 2021-04-22:
It should be possible to change the code for stepper motors. Just replace the Disqc part with the same general code as for the elevation. Unfortunately, I don't have any example code for stepper motors.

Closed 2021-04-27.

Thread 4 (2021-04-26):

Not working :(

luftpumpe83, 2021-04-26:
Hi,
I've ordered five PCBs at JLCPCB and soldered one of them with the parts.
But almost nothing is working. Automatic mode does nothing.
Tried to rotate the dish by pressing the buttons in the web interface and then the dish is moving in small steps - okay.
But the motor for elevation is not moving when pressing the up and down buttons.
Azimut and Elevation both showing "0.0°" - maybe there is no data from the sensors?
Because I ordered five pieces of every part (except the voltage regulator) I was able to build the whole circuit on a breadboard. But this also doesn't work (same result as before).
I've absolutely no idea what could be wrong. I changed SDA and SCL cables, but it keeps the same result.
In your circuit sheet there is a bridge between GND and AD0 on the gyroscope. Is that correct? I've tried it, but there is still no function.
Maybe I've made an obvious mistake, but I don't know, what it could be.
Thank you for your help.

luftpumpe83, 2021-04-26:
My failure... something went wrong when changing the code for AP mode.
Tried again with unmodified code and now it's working.

Closed 2021-04-26.

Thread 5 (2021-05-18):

Motoren bewegen sich nicht

ratzl, 2021-05-18:
Hallo,

ich habe die Platine nachgebaut und bin gerade bei der Inbetriebnahme.

Die beiden Sensorboards sind noch nicht angeschlossen.

Wenn ich im Webinterface auf AutoOFF schalte und die Schieber bewege reagieren die Motoren nicht.

Ich habe auch schon das Signal vom Rotor angeschaut, die Frequenz ist 27khz anstatt 22khz.

Was mache ich falsch?

Viele Grüße
Matthias

AK-Homberger, 2021-05-18:
Hallo Matthias,

ohne die Sensor-Boards habe ich das noch nie ausprobiert. Nach kurzer Sichtung des Codes sollte es aber gehen (Aber ohne absolute Gewähr).

Der Rotor sollte sich bei "Auto:Off" mit dem Rotor-Schiber bewegen lassen.

Der Linearmotor aber nicht. Dadurch das er kein Lagesignal hat, hat er keine Referenz und "Motor Error" ist zu hoch.

Wie hast du denn die Frequenz gemessen? Das Signal wird durch Zählen der der Microsecunden erzeugt:

void write0() {                      // write a '0' bit toneburst
  for (int i = 1; i <= 22; i++) {    // 1 ms of 22 kHz (22 cycles)
    digitalWrite(datapin, HIGH);
    delayMicroseconds(16);
    digitalWrite(datapin, LOW);
    delayMicroseconds(17);
  }
  delayMicroseconds(500);             // 0.5 ms of silence
}

Wenn die Frequenz nicht stimmt, kann das eigentlich nur dadurch kommen, dass das Timing des ESP8266 gestört ist. Eventuell durch das Fehlen der Sensoren.

Du kannst den Rotor-Code ja einmal in einem kleinnen eigenen Sketch laufen lassen.

Viele Grüße
Andreas

ratzl, 2021-05-19:
Hallo Andreas,

Ich habe das Signal mit einem Oszi gemessen.

Der Code den du gepostet hast, erzeugt doch aber eher einen Toneburst mit einer Frequenz von ca. 1(16us+17us) = 30303 Hz und einer Dauer von 22x(16us+17us)= 7.26ms ?

Sobald die Sensoren da sind werde ich noch mal berichten

Grüße
Matthias

AK-Homberger, 2021-05-19:
Deine Berechnung ist so nicht OK. Schau dir am Besten mal die verlinkte Diseqc-Spezifikation an (Datei: simple_tone_burst_detec.pdf im ZIP-File). Dann wird es bestimmt klarer.

ratzl, 2021-05-19:
Hier das Signal

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

ratzl, 2021-05-19:
Erstes Bild war im Leerlauf
Folgende Bilder mit angeschlossenem Motor

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

AK-Homberger, 2021-05-19:
Ich hab mir den Code nochmal angesehen. Die Quelle (Solartracker) lief auf einem langsameren Arduino. Für den schnelleren ESP8266 sind die Zeiten (16/17 Mikrosekunden) zu kurz. Erhöhe die mal schrittweise bis es passt (ca. 20 bis 25).

Und danke für den Hinweis. Es hat zwar bei mir trotzdem funktioniert. Mit 27.55 kHz Ist das aber doch etwas weit aus der Spezifikation.

Kanst du mir die finalen Werte senden. Mein Hameg kann leider keine automatische Frequenzanzeige.

Ich werde das Programm und die Dokumentation dann entsprechend anpassen.

ratzl, 2021-05-19:
Habe jetzt mal den Code so angepasst wie ich das verstehe, jetzt kann ich den Motor bewegen.
Ich habe auch nicht den exakt gleichen Motor verwendet wie in deinem Link(der ist nämlich nicht mehr verfügbar) Ich vermute dein Motor kommt auch mit 27khz zurecht.

Hier meine Änderung:

void write0() {                      // write a '0' bit toneburst
  for (int i = 1; i <= 22; i++) {    // 1 ms of 22 kHz (22 cycles)
    digitalWrite(datapin, HIGH);
    delayMicroseconds(22);
    digitalWrite(datapin, LOW);
    delayMicroseconds(23);
  }
  delayMicroseconds(500);             // 0.5 ms of silence
}

void write1() {                      // write a '1' bit toneburst
  for (int i = 1; i <= 11; i++) {    // 0.5 ms of 22 kHz (11 cycles)
    digitalWrite(datapin, HIGH);
    delayMicroseconds(22);
    digitalWrite(datapin, LOW);
    delayMicroseconds(23);
  }
  delayMicroseconds(1000);            // 1 ms of silence
}
1/45us = 22222khz,  und davon 22 Zyklen ergeben 1ms, bzw. 11 Zyklen = 0,5ms

ratzl, 2021-05-19:
die 22 bzw. 23 ergeben dann gemessen am Oszi 20,7 khz, das liegt innerhalb der Spec

AK-Homberger, 2021-05-19:
Ich setze dann beide auf 22. Das sollte noch etwas näher dran sein. Funktioniert jetzt der Motor?

ratzl, 2021-05-19:
Ja der Rotor dreht, jetzt warte ich noch auf die Sensoren.

Vielen Dank ;)

Closed 2021-05-19.

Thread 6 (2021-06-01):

GY-271

ratzl, 2021-06-01:
Hallo Andreas,

ich habe bereits bei zwei verschiedenen Lieferanten den GY-271 bestellt, leider ist darauf immer der  HMC5883L Chip verbaut, auch bei AZ-Delivery. Nach Rückfrage bei AZ-Delivery  wurde mir mitgeteilt , dass sie nur noch den auf Lager haben. Könntest du evtl. den Code so anpassen, dass auch der  HMC5883L Chip funktioniert?

Viele Grüße
Matthias

AK-Homberger, 2021-06-04:
Hallo Matthias,
da ich kein Device mit dem Chip habe, kann ich es leider nicht testen. Aber sehe dir doch einfach die Beispiele in der Bibliothek für den HMC5883L an. Du musst nur die Include-Datei, die Initialisierung in setup() und die Funktion für die Richtung austauschen. Ich bin sicher, das schaffst du auch selbst.
Viele Grüße
Andreas

joalbauer, 2021-06-05:
Hallo Matthias,
ich habe einen GY-271 bei makershop bestellt und einen GY-271 mit **Q**MC5883 Chip bekommen für 4,75€ Versand war ab 10€ kostenlos und auch recht zügig. [https://www.makershop.de/sensoren/gy-271-hmc5883l/](url)

Ich habe gelesen, dass der **H**MC5883L Chip von Honeywell gar nicht mehr produziert wird und deshalb viele auf den "Q-Chip" ausweichen, der hat aber eine andere I2C ID und wird anscheinend auch anders angesprochen, so dass die beiden Chips nicht direkt kompatibel sind.
Gruß Jochen

ratzl, 2021-06-09:
Hallo Jochen,
danke für den Tipp, habe den GY-271 schon bekommen.
Preis und Versand sind Top.
Grüße
Matthias

Closed 2021-07-05.

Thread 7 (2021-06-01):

Feature request: Add support for GPS module for automatic calculation of sat positioning data from latitude & longitude

joalbauer, 2021-06-01:
Awesome project! I have started to build a dish myself. While looking through my electronics parts box I stumbled upon an old GPS module. To take automation further ahead I would like to suggest adding support for GPS modules. Modules supporting 3.3V TTL level and NMEA protocol (9600bps serial connection if I remember correctly) are readily available at ebay or amazon for around 20€ . With the latitude and longitude determined via GPS it should be possible to calculate the required positioning data (i.e. azimuth and elevation) for the satellite of your choice without having to enter these data manually any more. I could try to find a way to implement such a function myself. But first I need to finish my built with the current version.

AK-Homberger, 2021-06-12:
Feel free to fork the project and implement the calculation by yourself. I don't see the need for such a feature currently, bacause I'm not travelling long distances that would require this function.

Closed 2021-06-12.

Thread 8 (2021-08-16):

AzimutOffset

dewilldi, 2021-08-16:
Im Artikel der Make von 2/2021 steht auf Seite 58 "Die Abweichung für den Kompasswird dann bei AzimutOffser eingetragen". Das hört sich ganz einfach an, ich habe es aber nicht hinbekommen. Habe den AzimutOffset auf 0 gesetzt, habe die Automatik eingeschaltet, gewartet bis sich die Schüssel ausgerichtet hat, dann die Automatik mit R-Off ausgeschaltet und mit SETP+ bzw. -STEP die Schüssel korrekt ausgerichtet. Jetzt wird mir bei Rotor ein Wert angezeigt. Wird dieser einfach als AzimutOffset eingetragen und wenn ja mit welchem Vorzeichen?

AK-Homberger, 2021-08-17:
Hallo,
bei der aktuellen Programmversion muss nichts mehr im Programm geändert werden. Einfach den Offset im Fenster "Satfinder Settings" bei "Azimut Offset" eintragen.

Allerdings funktioniert das nicht mit Step+/Step- sondern mit "Delta Azimut" Up/Down.
Den Wert für die korrekte Ausrichtung dann bei "Azimut Offest" eintagen. Dann sollte die korrekte Ausrichtung bei "Delta Azimut"=0 vorhanden sein, wobei eventuell kleine Korrekturen mit Step+/Step- nötig sein können (bei R-Off). Man kann das beliebig oft ändern, bis es passt.

Viele Grüße
Andreas

Closed 2021-11-01.

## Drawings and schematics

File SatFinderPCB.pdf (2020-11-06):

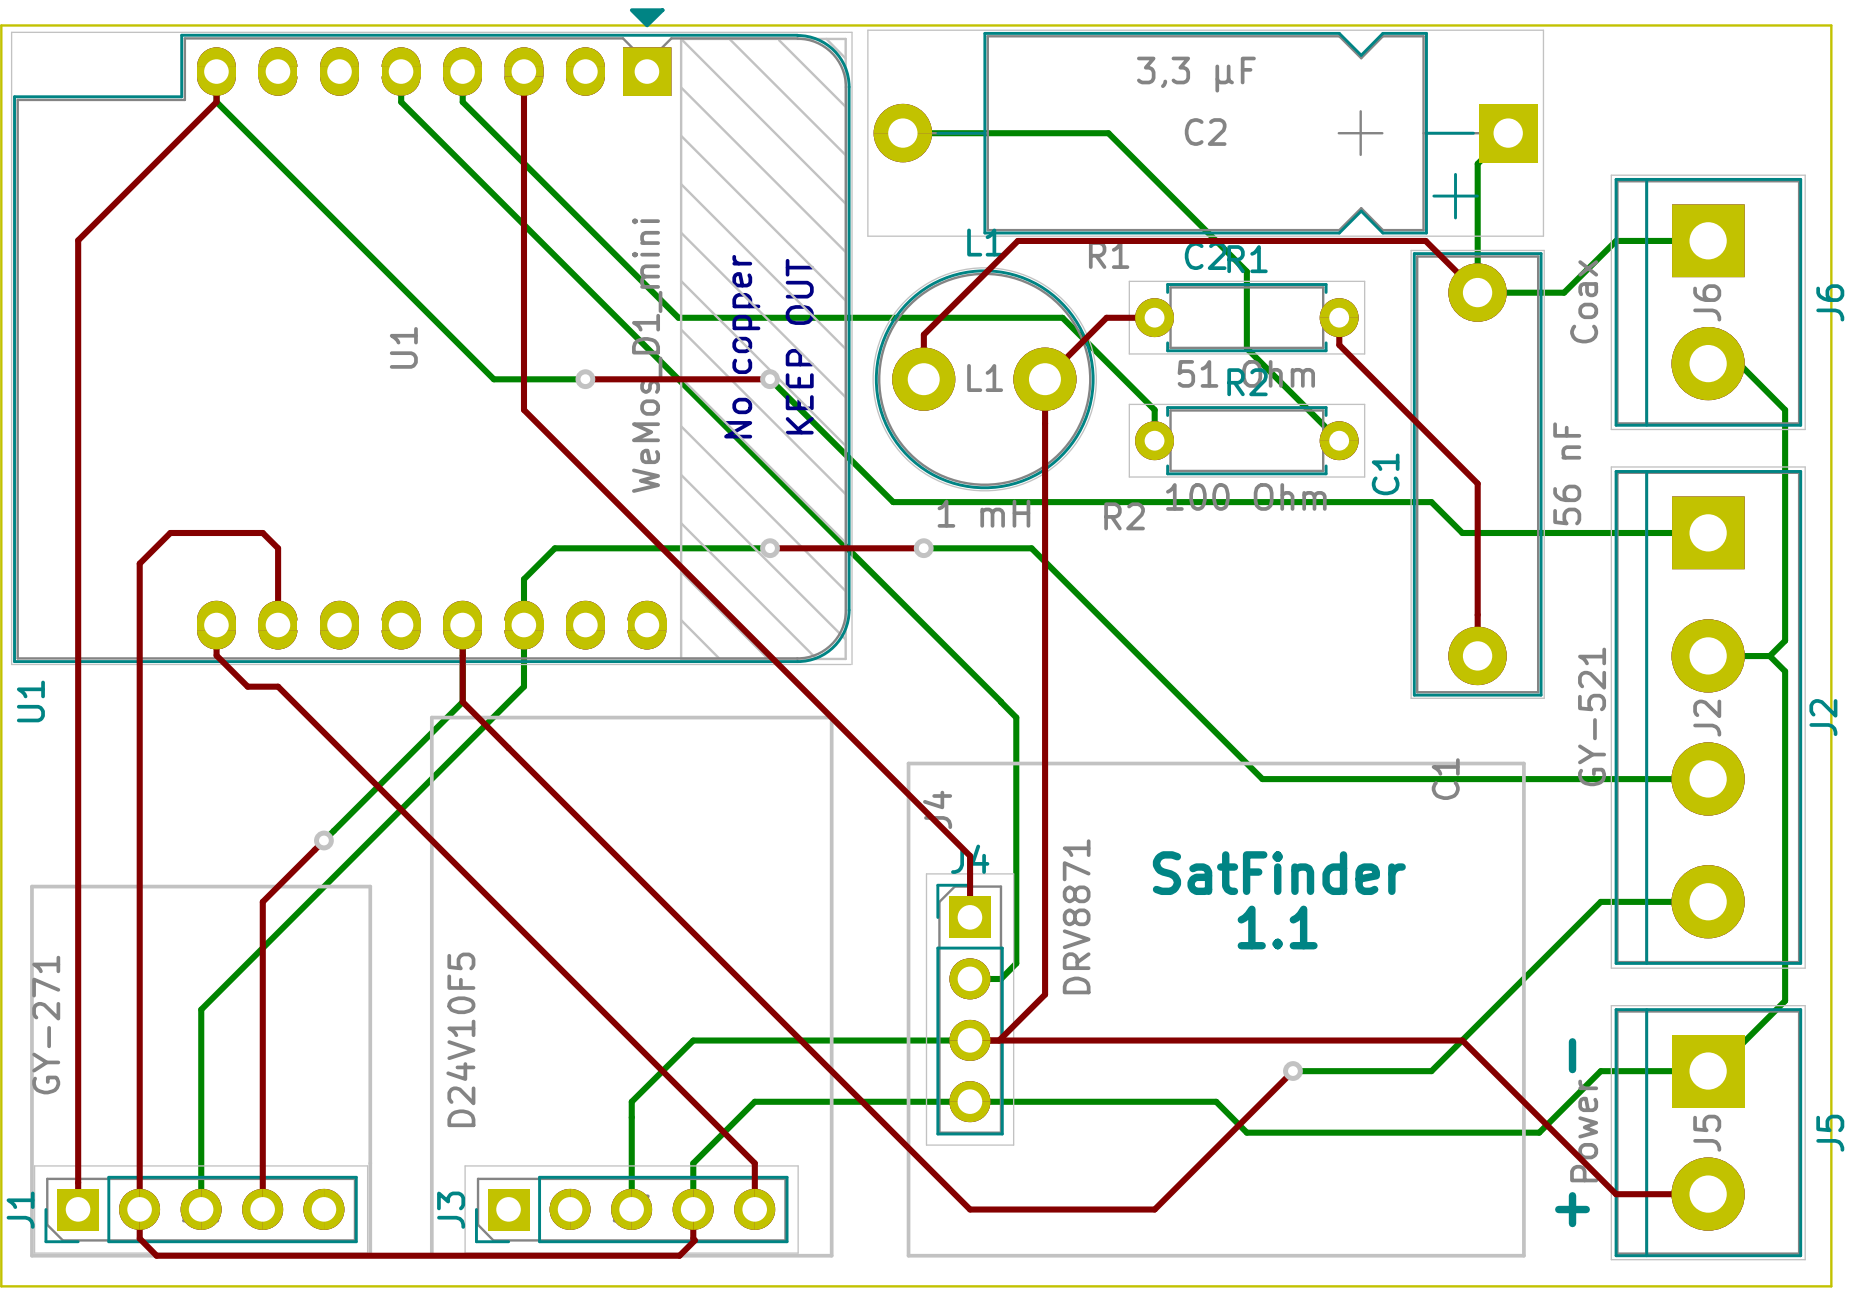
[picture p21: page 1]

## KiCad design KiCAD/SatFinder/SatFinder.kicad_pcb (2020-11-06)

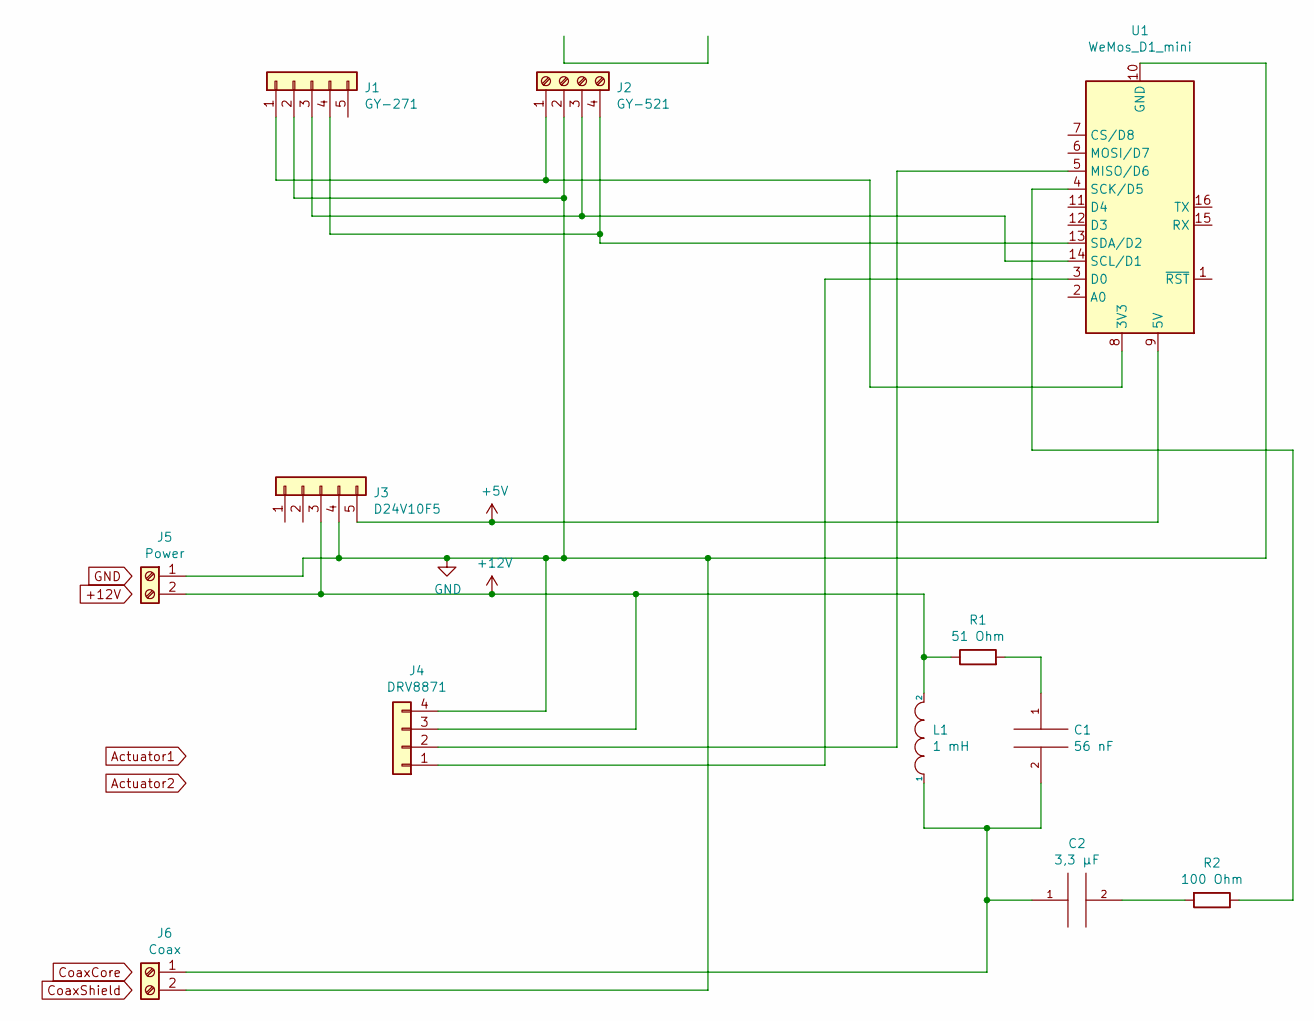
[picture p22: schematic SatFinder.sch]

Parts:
C1: 56 nF; C_Rect_L18.0mm_W5.0mm_P15.00mm_FKS3_FKP3
C2: 3,3 µF; CP_Axial_L18.0mm_D8.0mm_P25.00mm_Horizontal
J1: GY-271; PinHeader_1x05_P2.54mm_Vertical
J2: GY-521; TerminalBlock_bornier-4_P5.08mm
J3: D24V10F5; PinHeader_1x05_P2.54mm_Vertical
J4: DRV8871; PinHeader_1x04_P2.54mm_Vertical
J5: Power; TerminalBlock_bornier-2_P5.08mm
J6: Coax; TerminalBlock_bornier-2_P5.08mm
L1: 1 mH; L_Radial_D8.7mm_P5.00mm_Fastron_07HCP
R1: 51 Ohm; R_Axial_DIN0207_L6.3mm_D2.5mm_P7.62mm_Horizontal
R2: 100 Ohm; R_Axial_DIN0207_L6.3mm_D2.5mm_P7.62mm_Horizontal
U1: WeMos_D1_mini; WEMOS_D1_mini_light

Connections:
+5V: J3.5, U1.9 (5V)
+12V: J3.3, J4.3, J5.2, L1.2, R1.1
GND: J1.2, J2.2, J3.4, J4.4, J5.1, J6.2, U1.10 (GND)
unnamed: C1.1, R1.2
unnamed: C1.2, C2.1, J6.1, L1.1
unnamed: C2.2, R2.2
unnamed: J1.1, J2.1, U1.8 (3V3)
unnamed: J1.3, J2.3, U1.14 (SCL/D1)
unnamed: J1.4, J2.4, U1.13 (SDA/D2)
unnamed: J4.1, U1.3 (D0)
unnamed: J4.2, U1.5 (MISO/D6)
unnamed: R2.1, U1.4 (SCK/D5)

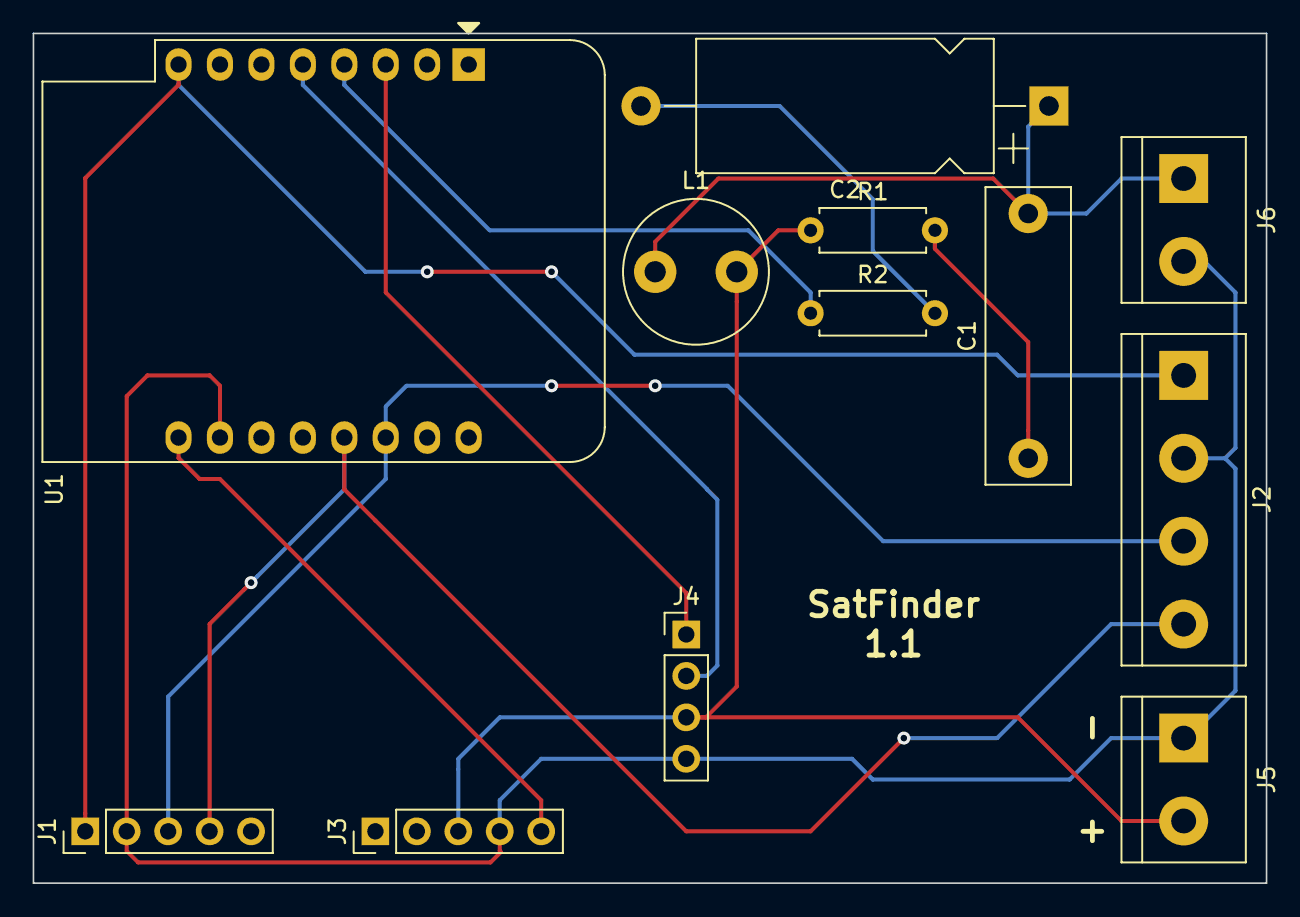
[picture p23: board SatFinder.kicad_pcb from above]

Board: 2 copper layers, 75.6 x 52.1 mm, 12 parts (0 on the bottom side), 12 nets.

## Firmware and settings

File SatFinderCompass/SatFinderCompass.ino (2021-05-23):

/*
  This code is free software; you can redistribute it and/or
  modify it under the terms of the GNU Lesser General Public
  License as published by the Free Software Foundation; either
  version 2.1 of the License, or (at your option) any later version.
  This code is distributed in the hope that it will be useful,
  but WITHOUT ANY WARRANTY; without even the implied warranty of
  MERCHANTABILITY or FITNESS FOR A PARTICULAR PURPOSE.  See the GNU
  Lesser General Public License for more details.
  You should have received a copy of the GNU Lesser General Public
  License along with this library; if not, write to the Free Software
  Foundation, Inc., 51 Franklin St, Fifth Floor, Boston, MA  02110-1301  USA
*/

// ESP8266 Diseqc SatFinder
// Controls satellite dish direction with Diseqc rotor (azimut) and linear actuator (elevation)
// Uses an MPU6050 device for Elevation and a QMC5883L compass for Azimut control.

// Version 1.1, 19.05.2021, AK-Homberger

#include <ESP8266WiFi.h>
#include <ESP8266WebServer.h>
#include <ArduinoJson.h>
#include <ESP8266WiFiGratuitous.h>
#include <ArduinoOTA.h>
#include <EEPROM.h>
#include <TinyMPU6050.h>
#include <QMC5883LCompass.h>

#include "index.h"  // Web page header file

//    SDA => D2
//    SCL => D1

#define datapin D5      // Digital pin for 22 kHz signal D5
#define motor1 D6       // Linear Actuator 1
#define motor2 D0       // Linear Actuator 2
#define UP 1
#define DOWN 2

#define Az_PCB_Correction 90  // Correction for compass direction of pcb mount

//Enter your SSID and PASSWORD
const char* ssid = "ssid";
const char* password = "password";

float Astra_Az = 164, Astra_El = 30.19, El_Offset = -18, Az_Offset = -10.0; // Astra 19.2 position and dish specific offsets

int motorSpeed = 700;  // Actuator speed     // Change (lower) this if dish is begining to swing

float Azimut = 0, Elevation = 0;
float sAzimut = 0, sElevation = 0;
float dAzimut = 0, dElevation = 0;
float IsRotor = 0, RotorPos = 0;

bool auto_on = false;
bool update_rotor = false;
bool rotor_changed = false;
bool rotor_off = false;

unsigned long comp_on_time = 0, motor_on_time = 0;

int motor_error = 0;
int LED_level = 0;

QMC5883LCompass compass;
MPU6050 mpu (Wire);

ESP8266WebServer server(80);

void setup(void) {
  bool LED = false;

  Serial.begin(115200);
  delay(1000);
  Serial.println();
  Serial.println("Initialise Compass and MPU...");

  compass.init();
  compass.setCalibration(-1598, 1511, -2365, 872, -1417, 1440);   // Do a calibration for the compass and put your values here!!!
  compass.setSmoothing(10, true);

  // MPU Initialization
  mpu.Initialize();
  //Serial.println("Starting calibration...");
  //mpu.Calibrate();
  //Serial.println("Calibration complete!");

  pinMode(datapin, OUTPUT);
  pinMode(motor1, OUTPUT);
  pinMode(motor2, OUTPUT);
  digitalWrite(motor1, HIGH);
  digitalWrite(motor2, HIGH);
  pinMode(D4, OUTPUT);
  digitalWrite(D4, HIGH);

  // ESP connects to your wifi
  WiFi.mode(WIFI_STA);
  WiFi.hostname("SatFinder");
  WiFi.begin(ssid, password);

  Serial.print("Connecting to ");
  Serial.print(ssid);

  // Wait for WiFi to connect
  while (WiFi.status() != WL_CONNECTED) {
    Serial.print(".");
    delay(500);
    digitalWrite(D4, LED);
    LED = ! LED;
  }
  digitalWrite(D4, HIGH);

  // If connection successful show IP address in serial monitor
  Serial.println("");
  Serial.print("Connected to ");
  Serial.println(ssid);
  Serial.print("IP address: ");
  Serial.println(WiFi.localIP());  //IP address assigned to your ESP

  experimental::ESP8266WiFiGratuitous::stationKeepAliveSetIntervalMs(5000);

  // Arduino OTA config and start
  ArduinoOTA.setHostname("Satfinder");
  ArduinoOTA.begin();

  server.on("/", handleRoot);      //This is display page
  server.on("/get_data", handleGetData);//To get update of values
  server.on("/on", handleOn);
  server.on("/off", handleOff);
  server.on("/r_off", handleRotorOff);
  server.on("/az_up", handleAzUp);
  server.on("/az_down", handleAzDown);
  server.on("/el_up", handleElUp);
  server.on("/el_down", handleElDown);
  server.on("/rotor_up", handleRotorUp);
  server.on("/rotor_down", handleRotorDown);
  server.on("/rotor_up_step", handleRotorUpStep);
  server.on("/rotor_down_step", handleRotorDownStep);
  server.on("/cal", handleCal);

  server.on("/slider1", handleSlider1);
  server.on("/slider2", handleSlider2);
  server.on("/slider3", handleSlider3);

  server.on("/settings", handleSettings);
  server.on("/get_settings", handleGetSettings);
  server.on("/set_settings", handleSetSettings);

  server.onNotFound(handleNotFound);

  server.begin();                  //Start server
  Serial.println("HTTP server started");

  EEPROM.begin(128);
  float tmp = 0;

  EEPROM_Read(&tmp, 0);
  if ((tmp >= 90) && (tmp <= 270)) Astra_Az = tmp;

  EEPROM_Read(&tmp, sizeof(float));
  if ( (tmp >= 10) && (tmp < 50) ) Astra_El = tmp;

  EEPROM_Read(&tmp, sizeof(float) * 2);
  if (abs(tmp) < 90) El_Offset = tmp;

  EEPROM_Read(&tmp, sizeof(float) * 3);
  if (abs(tmp) < 90) Az_Offset = tmp;

  EEPROM_Read(&tmp, sizeof(float) * 4);
  if ((tmp >= 500) && (tmp < 1024)) motorSpeed = trunc(tmp);

  sAzimut = Astra_Az;
  sElevation = Astra_El;
}


void handleRoot() {
  server.send(200, "text/html", MAIN_page); //Send web page
}

void handleSettings() {
  server.send(200, "text/html", Settings_page); //Send settings web page
}


void handleGetSettings() {
  String Text;

  StaticJsonDocument<300> root;

  root["azimut"] = Astra_Az;
  root["elevation"] = Astra_El;
  root["el_offset"] = El_Offset;
  root["az_offset"] = Az_Offset;
  root["motor_speed"] = motorSpeed;

  serializeJsonPretty(root, Text);
  server.send(200, "text/plain", Text); //Send values to client ajax request
}


void handleSetSettings() {
  float tmp;

  if (server.args() > 3) {

    tmp = server.arg(0).toFloat();
    if ((tmp >= 90) && (tmp <= 270)) Astra_Az = tmp;

    tmp = server.arg(1).toFloat();
    if ( (tmp >= 10) && (tmp <= 50) ) Astra_El = tmp;

    tmp = server.arg(2).toFloat();
    if (abs(tmp) <= 90) El_Offset = tmp;

    tmp = server.arg(3).toFloat();
    if (abs(tmp) <= 90) Az_Offset = tmp;

    tmp = server.arg(4).toFloat();
    if ((tmp >= 500) && (tmp < 1024)) motorSpeed = trunc(tmp);
  }

  EEPROM_Write(&Astra_Az, 0);
  EEPROM_Write(&Astra_El, sizeof(float));
  EEPROM_Write(&El_Offset, sizeof(float) * 2);
  EEPROM_Write(&Az_Offset, sizeof(float) * 3);
  EEPROM_Write(&tmp, sizeof(float) * 4);

  EEPROM.commit();
  server.send(200, "text/html");
}


void handleGetData() {
  String Text;

  StaticJsonDocument<300> root;

  root["azimut"] = Azimut;
  root["elevation"] = Elevation;

  root["s_azimut"] = sAzimut;
  root["s_elevation"] = sElevation;

  root["d_azimut"] = dAzimut;
  root["d_elevation"] = dElevation;

  root["rotor"] = IsRotor;
  root["led_level"] = LED_level;

  if (auto_on) root["state"] = "On"; else root["state"] = "Off";
  if (auto_on && rotor_off) root["state"] = "R-Off";

  serializeJsonPretty(root, Text);
  server.send(200, "text/plain", Text); //Send sensors values to client ajax request
}


void handleCal() {
  Serial.println("Starting calibration...");
  mpu.Calibrate();
  Serial.println("Calibration complete!");
  server.send(200, "text/html");
}


void handleAzDown() {
  if (dAzimut > -50) dAzimut -= 0.5;
  update_rotor = true;
  server.send(200, "text/html");
}


void handleAzUp() {
  if (dAzimut < 50) dAzimut += 0.5;
  update_rotor = true;
  server.send(200, "text/html");
}


void handleElDown() {
  if (dElevation > -8) dElevation -= 0.1;
  server.send(200, "text/html");
}


void handleElUp() {
  if (dElevation < 8) dElevation += 0.1;
  server.send(200, "text/html");
}


void handleRotorDown() {
  if (RotorPos > -70) RotorPos -= 1;
  update_rotor = true;
  server.send(200, "text/html");
}


void handleRotorUp() {
  if (RotorPos < 70) RotorPos += 1;
  update_rotor = true;
  server.send(200, "text/html");
}


void handleRotorDownStep() {
  noInterrupts();
  write_byte_with_parity(0xE0);
  write_byte_with_parity(0x31);
  write_byte_with_parity(0x69);
  write_byte_with_parity(0xfe);
  interrupts();
  server.send(200, "text/html");
  comp_on_time = millis() + 1000;
  rotor_changed = true;
  IsRotor = IsRotor + 1.0 / 8.0;
}


void handleRotorUpStep() {
  noInterrupts();
  write_byte_with_parity(0xE0);
  write_byte_with_parity(0x31);
  write_byte_with_parity(0x68);
  write_byte_with_parity(0xfe);
  interrupts();
  server.send(200, "text/html");
  comp_on_time = millis() + 1000;
  rotor_changed = true;
  IsRotor = IsRotor - 1.0 / 8.0;
}



void handleOn() {
  digitalWrite(D4, LOW);
  server.send(200, "text/html");
  auto_on = true;
  rotor_off = false;
  motor_error = 0;
}


void handleOff() {
  auto_on = false;
  rotor_off = true;
  digitalWrite(D4, HIGH);
  server.send(200, "text/html");
  noInterrupts();
  write_byte_with_parity(0xE0);
  write_byte_with_parity(0x31);
  write_byte_with_parity(0x60);
  interrupts();
  comp_on_time = 0;
  digitalWrite(motor2, HIGH);
  digitalWrite(motor1, HIGH);
}


void handleRotorOff() {
  rotor_off = true;

  server.send(200, "text/html");

  noInterrupts();
  write_byte_with_parity(0xE0);
  write_byte_with_parity(0x31);
  write_byte_with_parity(0x60);
  interrupts();
  comp_on_time = 0;
  digitalWrite(motor2, HIGH);
  digitalWrite(motor1, HIGH);
}



void handleSlider1() {
  if (server.args() > 0) {
    dAzimut =  server.arg(0).toFloat();
    Serial.print("Azimut:");
    Serial.println(Azimut);
    //update_rotor = true;
  }
  server.send(200, "text/html");
}


void handleSlider2() {
  if (server.args() > 0) {
    dElevation = server.arg(0).toFloat();
    Serial.print("Elevation:");
    Serial.println(Elevation);
  }
  server.send(200, "text/html");
}


void handleSlider3() {
  if (server.args() > 0) {
    RotorPos = server.arg(0).toFloat();
    Serial.print("Rotor:");
    Serial.println(RotorPos);
    update_rotor = true;
  }
  server.send(200, "text/html");
}


void handleNotFound() {                                           // Unknown request. Send error 404
  server.send(404, "text/plain", "File Not Found\n\n");
}

void EEPROM_Write(float *num, int MemPos)
{
  byte ByteArray[4];
  memcpy(ByteArray, num, 4);
  for (int x = 0; x < 4; x++)
  {
    EEPROM.write((MemPos * 4) + x, ByteArray[x]);
  }
}

void EEPROM_Read(float *num, int MemPos)
{
  byte ByteArray[4];
  for (int x = 0; x < 4; x++)
  {
    ByteArray[x] = EEPROM.read((MemPos * 4) + x);
  }
  memcpy(num, ByteArray, 4);
}


void write0() {                      // write a '0' bit toneburst
  for (int i = 1; i <= 22; i++) {    // 1 ms of 22 kHz (22 cycles)
    digitalWrite(datapin, HIGH);
    delayMicroseconds(21);
    digitalWrite(datapin, LOW);
    delayMicroseconds(21);
  }
  delayMicroseconds(500);             // 0.5 ms of silence
}


void write1() {                      // write a '1' bit toneburst
  for (int i = 1; i <= 11; i++) {    // 0.5 ms of 22 kHz (11 cycles)
    digitalWrite(datapin, HIGH);
    delayMicroseconds(21);
    digitalWrite(datapin, LOW);
    delayMicroseconds(21);
  }
  delayMicroseconds(1000);            // 1 ms of silence
}


// Calculate parity of a byte
bool parity_even_bit(byte x) {
  unsigned int count = 0, i, b = 1;

  for (i = 0; i < 8; i++) {
    if ( x & (b << i) ) {
      count++;
    }
  }
  if ( (count % 2) ) {
    return 0;
  }
  return 1;
}


// write the parity of a byte (as a toneburst)
void write_parity(byte x) {
  if (parity_even_bit(x)) write0(); else write1();
}


// write out a byte (as a toneburst)
// high bit first (ie as if reading from the left)
void write_byte(byte x) {
  for (int j = 7; j >= 0; j--) {
    if (x & (1 << j)) write1(); else write0();
  }
}


// write out a byte with parity attached (as a toneburst)
void write_byte_with_parity(byte x) {
  write_byte(x);
  write_parity(x);
}


// goto position angle a in degrees, south = 0.
// (a must be in the range +/- 75 degrees)
void goto_angle(float a) {
  /*
    Note the diseqc "goto x.x" command is not well documented.
    The general decription is available at https://de.eutelsat.com/en/support/technical-support/diseqc.html
    See "Positioner Application Note.pdf".

  */

  byte n1, n2, n3, n4, d1, d2;
  int a16;
  // get the angle in range +/- 75 degrees.  Sit at these limits and switch
  // over at ~ midnight unless otherwise instructed.

  if (a < -75.0) {
    a = -75;
  }
  if (a > 75.0) {
    a = 75;
  }

  // set the sign nibble in n1 to E (east) or D (west).
  if (a < 0) {
    n1 = 0xE0;
  } else {
    n1 = 0xD0;
  }
  // shift everything up so the fraction (1/16) nibble is in the
  //integer, and round to the nearest integer:
  a16 =  (int) (16.0 * abs(a) + 0.5);
  // n2 is the top nibble of the three-nibble number a16:
  n2 = (a16 & 0xF00) >> 8;
  // the second data byte is the bottom two nibbles:
  d2 = a16 & 0xFF;
  //the first data byte is
  d1 = n1 | n2;
  // send the command to the positioner
  noInterrupts();
  write_byte_with_parity(0xE0);
  write_byte_with_parity(0x31);
  write_byte_with_parity(0x6E);
  write_byte_with_parity(d1);
  write_byte_with_parity(d2);
  interrupts();
}


void motor(int direction) {
  float X = 0, Y = 0;

  mpu.Execute();
  X = round(mpu.GetAngX() * 10) / 10;

  if (direction == UP) {
    digitalWrite(motor2, LOW);
    analogWrite(motor1, motorSpeed);
    delay(10);
    mpu.Execute();
    Y = round(mpu.GetAngX() * 10) / 10;
  }

  if (direction == DOWN) {
    digitalWrite(motor1, LOW);
    analogWrite(motor2, motorSpeed - 500);
    delay(10);
    mpu.Execute();
    Y = round(mpu.GetAngX() * 10) / 10;
  }

  digitalWrite(motor1, HIGH);
  digitalWrite(motor2, HIGH);

  delay(10);
  //comp_on_time = millis() + 500;
  //rotor_changed = true;
  if ( X == Y ) motor_error++; else motor_error = 0;
}


void loop(void) {
  server.handleClient();
  ArduinoOTA.handle();
  mpu.Execute();
  compass.read();

  sAzimut = Astra_Az + dAzimut;
  sElevation = Astra_El + dElevation;

  dAzimut = round(dAzimut * 10) / 10;
  dElevation = round(dElevation * 10) / 10;

  sAzimut = round(sAzimut * 10) / 10;
  sElevation = round(sElevation * 10) / 10;

  if (rotor_changed && (millis() > comp_on_time )) {
    rotor_changed = false;
    Serial.println("Compass On");
  }

  if (!rotor_changed && !rotor_off)  {
    Azimut = compass.getAzimuth() - Az_PCB_Correction - Az_Offset;
    if (Azimut < 0) Azimut += 360;
    if (Azimut > 360) Azimut -= 360;
  }

  Elevation = -round((mpu.GetAngX() + El_Offset) * 10) / 10;
  if (Elevation < 0 ) Elevation = 0;

  if (auto_on) {
    RotorPos = sAzimut - Azimut;
    if (RotorPos > 70) RotorPos = 70;
    if (RotorPos < -70) RotorPos = -70;

    if (motor_error < 20) {
      if (sElevation - Elevation > 0.3) {
        motor(UP);
      }
      else if (sElevation - Elevation < -0.3) {
        motor(DOWN);
      }
    }
  }

  if ((!rotor_off && abs(RotorPos - IsRotor) > 1) || update_rotor) {
    comp_on_time = millis() + (abs(RotorPos - IsRotor) * 700);
    rotor_changed = true;

    goto_angle(-RotorPos);
    Serial.print("RotorPos: ");
    Serial.println(RotorPos);
    IsRotor = RotorPos;
    update_rotor = false;
  }
  delay(10);
}

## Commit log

2020-10-26 Added R-Off and corrected compass smoothing.
    [SatFinderCompass.ino]
2020-10-29 Added KiCAD files
    [SatFinder.kicad_pcb, SatFinder.sch]
2020-11-06 Version 1.1
    [SatFinder.kicad_pcb, SatFinder.sch]
2020-11-07 Corrected error in Azimut calculation (0-360).
    [SatFinderCompass.ino]
2020-11-07 Corrected error in azimut calculation.
    [SatFinderCompass.ino]
2021-04-05 Smaller connector for linear drive.
    [SatFinderUnten.scad]
2021-05-19 V1.1: Improved timing for 22 kHz signal generation.
    Changed delay microseconds from 16/17 to 22 to get 22 kHz signal. The solartracker source code worked on a slower Arduinon. The faster ES82666 needs different delay values.
2021-05-23 V1.1: Improved timing for 22 kHz signal generation.
    Changed delay microseconds from 16/17 to 21 to get 22 kHz signal. The solartracker source code worked on a slower Arduinon. The faster ES82666 needs different delay values.
